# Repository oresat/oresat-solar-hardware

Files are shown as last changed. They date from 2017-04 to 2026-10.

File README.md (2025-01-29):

# OreSat Solar Modules

This repo contains the CAD for [OreSat's](oresat.org) solar modules. Part of OreSat's design is a module bus system that spans 1 - 3 U, so each array is its own 1U "panel". Oresat0, a 1U CubeSat, thus has 4 solar modules, and OreSat1, a 2U CubeSat, has 8. This approach has pretty severe drawbacks in terms of solar cell coverage area, but it's extremely flexible for having one design across a bunch of different designs. One nifty part of this design is that each 1u panel has its own **true** maximum power point tracker, with a software-defined MPPT algorithm. We're MPPT elitists - we eschew maximum power point "controllers" and think if it's not doing true power point optimization, you're just doing it wrong.

That and coffee. You're all doing coffee wrong, too, but we don't hold that against you, you don't live in Portland, we understand.

We've flown our GaAs solar cell design, and are currently workingon our silicon design.

# Design Notes

**Status, design, construction, and testing information can be found in the [OreSat Solar Module Design Notes](https://docs.google.com/document/d/1mogZjYhJievwLsnVkg4Q0sEF9xPMA5q7KPciky3YWKE/edit?usp=sharing).**

# Pretty Pictures

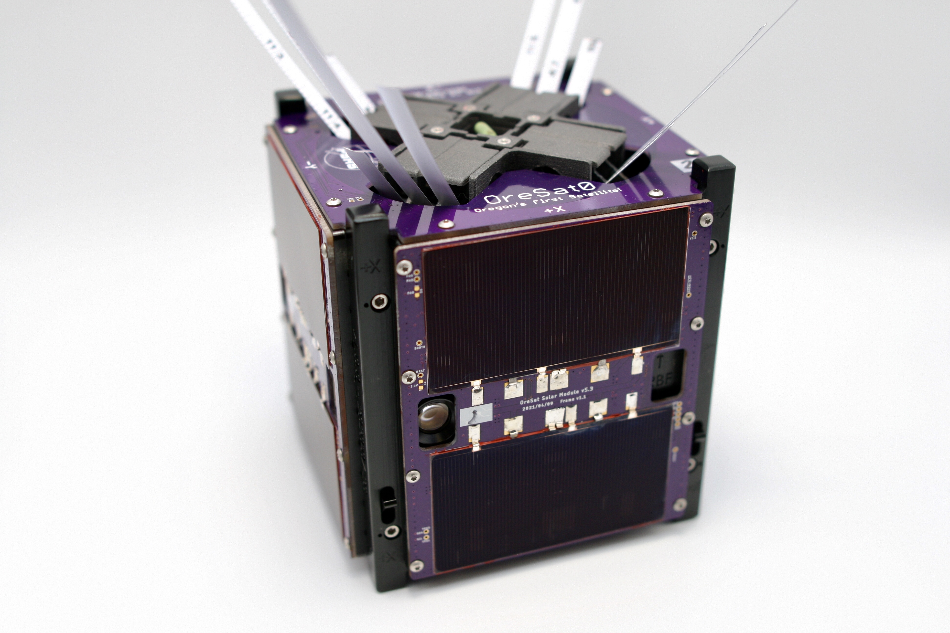
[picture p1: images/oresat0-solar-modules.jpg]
Solar modules on OreSat0

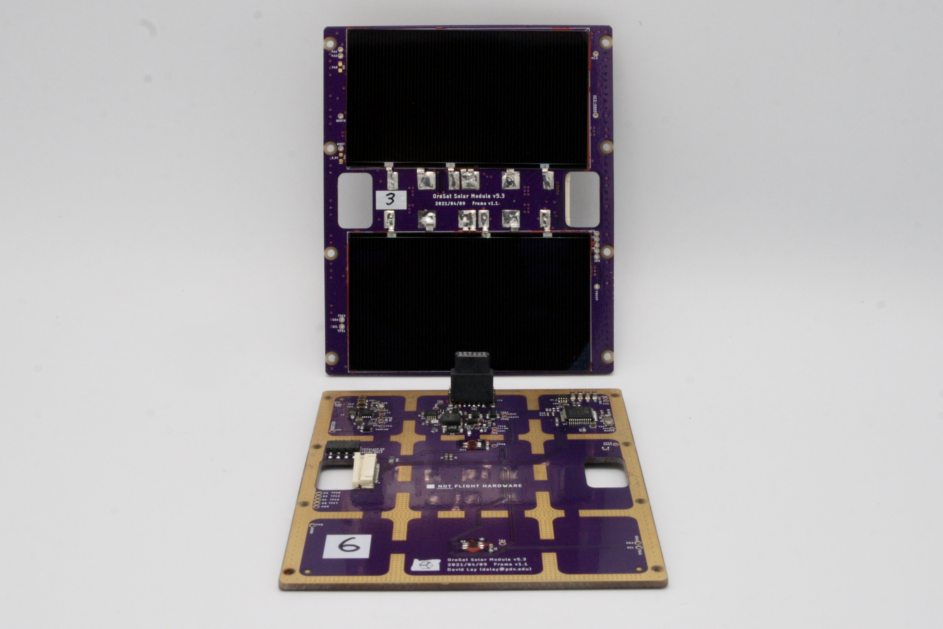
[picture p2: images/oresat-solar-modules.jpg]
Top (solar cells) and bottom (circuitry) of the solar modules


## LICENSE

Copyright the Portland State Aerospace Society, 2025.

This source describes Open Hardware that is licensed under CERN-OHL-S v2, or any later version.

You may redistribute and modify this source and make products using it under the terms of the CERN-OHL-S v2 (https://ohwr.org/cern_ohl_s_v2.txt).

This source is distributed WITHOUT ANY EXPRESS OR IMPLIED WARRANTY, INCLUDING OF MERCHANTABILITY, SATISFACTORY QUALITY AND FITNESS FOR A PARTICULAR PURPOSE. Please see the CERN-OHL-S v2 for applicable conditions.

Source location: https://github.com/oresat/

If you require a different license for this open hardware project, please contact us at [oresat@pdx.edu](mailto:oresat@pdx.edu).

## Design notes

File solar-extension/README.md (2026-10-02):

---
title: "**OreSat Solar Extension Board**"
subtitle: |
  **Fabrication and Assembly Information**\
  For build 2026-06-23T21-24-18
fontsize: 10pt
geometry:
  - margin=0.5in
toc: true
toc-depth: 2
colorlinks: true
urlcolor: blue
---

\newpage

# About this Board

## Board Description

This board connects the Oresat Solar Simulator to an OreSat engineering or development unit (specifically the End or Mid Cards). It allows us to plug HIL-run solar modules right into the engineering unit.

## Documentation Links

- Git repository: <https://github.com/oresat/oresat-solar-hardware>
- **TODO:** Design Notes + Design Review Notes

## Documentation Files

| Filename | Notes |
| --- | --- |
| README.pdf | This README file |
| flatsat-breakout-outline.dxf | Board outline (with holes) in DXF format |
| flatsat-breakout-pcba.step | 3D model of PCBA (with components) |
| flatsat-breakout-render-bot.jpg | Render of the top of the 3D model |
| flatsat-breakout-render-bot.jpg | Render of the bottom of the 3D model |
| flatsat-breakout-schematic.pdf | PDF of board schematics |

## Contact Information

- Website: <https://www.oresat.org/>
- Email: <oresat@pdx.edu>
- Instagram: @pdxaerospace

## Board Renders

Render of the top of the 3D model
Render of the bottom of the 3D model

\newpage

# Printed Circuit Board (PCB) Fabrication Information

## Board Info

- 2 layer board
- Bounding box is TBD
- Board thickness is 1.59 mm

## Board Requirements

- Design Rules
    - Minimum Trace / Space design rules
       - Outer layers: 0.127 mm (5.0 mil) / 0.127 mm (5.0 mil)
       - Inner layers: 0.127 mm (5.0 mil) / 0.127 mm (5.0 mil)
    - Outer dimension router tolerance: +/- 0.254 mm (10.0 mil)
    - Hole placement tolerance: +/- 0.075 mm (3.0 mil)
    - Inner tab routed slot tolerance: +/- 0.254 mm (10.0 mil)
- Drills
   - Drill Positional Tolerance: 0.051 mm (2.0 mil)
   - Drill Size tolerance: +/- 0.064 mm (2.5 mil)
- Plated/Un-plated holes
  - Via/PTH minimum diameter: 0.254 mm (10 mil)
  - Via/PTH minimum annulus: 0.102 mm (4 mil) radius
- Outline/Routing
  - No requirements
- Slots
  - There are no slots.
- Cutouts
  - There are no cutouts
- There are 3 fiducials on the top layer.
- Panel tabs ("mouse bites")
   - Card edges must be smooth; no mouse bites or other intrusions into the card outline.
   - If external mouse bites are required, minimize and customer will remove by hand before assembly.
- If not otherwise specified, build to IPC 6012 Class 2 or better.

## Stackup /  Materials

- Outside copper layers is 1 oz Cu after plating (0.043 mm / 1.7 mil)
- Inside copper layers are 0.5 oz Cu (0.018 mm / 0.7 mil)
- There are no requirements on the prepreg or core of this four layer stackup.
- Board Surface treatment should be ENIG, althogh immersion Silver is acceptable.
- White silkscreen on top and bottom surface
- Taiyo PSR-4000 or equivalent soldermask on top and bottom, no requirements for color.

## Array / Panel Information

- Coordinate with Contract Manufacturer (CM) for optimal size of this panel.
- If no feedback from CM, then produce single boards (no panel).

## Fabrication Files

### IPC-2581 File

| Filename | Notes |
| --- | --- |
| flatsat-breakout-ipc2581.xml | IPC-2581 board information file |

### Legacy PCB Files

| Filename | Notes |
| ---| --- |
| flatsat-breakout-Edge_Cuts.gbr | RS274X file for the dimension (outline) layer |
| flatsat-breakout-F_Silkscreen.gbr | RS274X file for the top silkscreen |
| flatsat-breakout-F_Mask.gbr | RS274X file for the top soldermask |
| flatsat-breakout-F_Cu.gbr | RS274X file for the top copper layer |
| flatsat-breakout-In1_Cu.gbr | RS274X file for the layer 2 copper |
| flatsat-breakout-In2_Cu.gbr | RS274X file for the layer 3 copper |
| flatsat-breakout-B_Cu.gbr | RS274X file for the bottom copper layer |
| flatsat-breakout-B_Mask.gbr | RS274X file for the bottom soldermask |
| flatsat-breakout-B_Silkscreen.gbr | RS274X file for the bottom silkscreen |
| flatsat-breakout-NPTH.drl | Excellon file for non-plated through holes |
| flatsat-breakout-PTH.drl | Excellon file for plated through holes | 

\newpage

# Printed Circuit Board Assembly (PCBA) Information

## Assembly Info

- This PCBA uses both surface mount (SMT) and through-hole (THT) components.

## Assembly Requirements

- Assemble to IPC Class 2 or better
- Bake components that are not moisture sealed to appropriate levels as required.
- Any solder paste (leaded or RoHS) is acceptable. RoHS solder is slightly preferred.
- Any no-clean or aqueous wash flux is acceptable.
- No conformal coating.

## Component Specific Assembly Information

- No specific information

## Assembly Files

### IPC-2581 File

| Filename | Notes |
| --- | --- |
| flatsat-breakout-ipc2581.xml | IPC-2581 board information file |

### Bill of Materials (BOM)

| Filename | Description |
| --- | --- |
| flatsat-breakout-bom.csv | BOM in Comma Separated Variable format |

### Solder Paste Stencils

| Filename | Notes |
| --- | --- |
| flatsat-breakout-B_Paste.gbr | RS274X file for top/front solder paste stencil |
| flatsat-breakout-F_Paste.gbr | RS274X file for bottom/back solder paste stencil |

### Mounting/Placement Location

| Filename | Description |
| --- | --- |
| flatsat-breakout.pos | Pick and place locations for components |

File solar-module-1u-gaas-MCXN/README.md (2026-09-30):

---
title: "**OreSat Solar Module with GaAs Cells and MCXN processor**"
subtitle: |
  **Fabrication and Assembly Information**\
  For build TIME-STAMP
fontsize: 10pt
geometry:
  - margin=0.5in
toc: true
toc-depth: 2
colorlinks: true
urlcolor: blue
---

\newpage

# About this Board

## Board Description

This PCB is for the OreSat "1U" solar module which is used for all OreSat 1 - 3U designs. It has GaAs and Si solar cell variants, as well as STM32 and MCXN microcontorller variants. This design is the GaAs + MCXN version. It is scheduled to fly on OreSat1. 

The solar module takes power from the solar cells and does true maximum power point tracking (MPPT) using the Perturb and Observe ("P&O") method. It boosts the cell voltage up to 8.2 V in order to directly charge the batteries.

## Documentation Links

- Git repository: <https://github.com/oresat/oresat-solar-hardware>
- [Design Notes](https://docs.google.com/document/d/1mogZjYhJievwLsnVkg4Q0sEF9xPMA5q7KPciky3YWKE/edit?usp=sharing)

## Documentation Files

| Filename | Notes |
| --- | --- |
| README.pdf | This README file |
| PROJECT-NAME-outline.dxf | Board outline (with holes) in DXF format |
| PROJECT-NAME-pcba.step | 3D model of PCBA (with components) |
| PROJECT-NAME-render-bot.jpg | Render of the top of the 3D model |
| PROJECT-NAME-render-bot.jpg | Render of the bottom of the 3D model |
| PROJECT-NAME-schematic.pdf | PDF of board schematics |

## Contact Information

- Website: <https://www.oresat.org/>
- Email: <oresat@pdx.edu>
- Instagram: @pdxaerospace

## Board Renders

Render of the top of the 3D model
Render of the bottom of the 3D model

\newpage

# Printed Circuit Board (PCB) Fabrication Information

## Board Info

- 4 layer board
- Bounding box is 83.0 x 100.0 mm
- Board thickness is 1.59 mm

## Board Requirements

- Design Rules
    - Minimum Trace / Space design rules
       - Outer layers: 0.127 mm (5.0 mil) / 0.127 mm (5.0 mil)
       - Inner layers: 0.127 mm (5.0 mil) / 0.127 mm (5.0 mil)
    - Outer dimension router tolerance: +/- 0.254 mm (10.0 mil)
    - Hole placement tolerance: +/- 0.075 mm (3.0 mil)
    - Inner tab routed slot tolerance: +/- 0.254 mm (10.0 mil)
- Drills
   - Drill Positional Tolerance: 0.051 mm (2.0 mil)
   - Drill Size tolerance: +/- 0.064 mm (2.5 mil)
- Plated/Un-plated holes
  - Via/PTH minimum diameter: 0.254 mm (10 mil)
  - Via/PTH minimum annulus: 0.102 mm (4 mil) radius
- Outline/Routing
  - This board requires a 1 mm router bit.
- Slots/Cutouts
  - There are six cutouts in the board.
- There are 3 fiducials on the top layer.
- Panel tabs ("mouse bites")
   - Card edges must be smooth; no mouse bites or other intrusions into the card outline.
   - If external mouse bites are required, minimize and customer will remove by hand before assembly.
- If not otherwise specified, build to IPC 6012 Class 2 or better.

## Stackup /  Materials

- Outside copper layers is 1 oz Cu after plating (0.043 mm / 1.7 mil)
- Inside copper layers are 0.5 oz Cu (0.018 mm / 0.7 mil)
- There are no requirements on the prepreg or core of this four layer stackup.
- Board Surface treatment should be ENIG, althogh immersion Silver is acceptable.
- White silkscreen on top and bottom surface
- Taiyo PSR-4000 or equivalent soldermask on top and bottom, no requirements for color.

## Array / Panel Information

- Coordinate with Contract Manufacturer (CM) for optimal size of this panel.
- If no feedback from CM, then produce single boards (no panel).

## Fabrication Files

### IPC-2581 File

| Filename | Notes |
| --- | --- |
| PROJECT-NAME-ipc2581.xml | IPC-2581 board information file |

### Legacy PCB Files

| Filename | Notes |
| ---| --- |
| PROJECT-NAME-Edge_Cuts.gbr | RS274X file for the dimension (outline) layer |
| PROJECT-NAME-F_Silkscreen.gbr | RS274X file for the top silkscreen |
| PROJECT-NAME-F_Mask.gbr | RS274X file for the top soldermask |
| PROJECT-NAME-F_Cu.gbr | RS274X file for the top copper layer |
| PROJECT-NAME-In1_Cu.gbr | RS274X file for the layer 2 copper |
| PROJECT-NAME-In2_Cu.gbr | RS274X file for the layer 3 copper |
| PROJECT-NAME-B_Cu.gbr | RS274X file for the bottom copper layer |
| PROJECT-NAME-B_Mask.gbr | RS274X file for the bottom soldermask |
| PROJECT-NAME-B_Silkscreen.gbr | RS274X file for the bottom silkscreen |
| PROJECT-NAME-NPTH.drl | Excellon file for non-plated through holes |
| PROJECT-NAME-PTH.drl | Excellon file for plated through holes | 

\newpage

# Printed Circuit Board Assembly (PCBA) Information

## Assembly Info

- All components are on the top side of the board.
- This PCBA uses only surface mount (SMT) components.

## Assembly Requirements

- Assemble to IPC Class 2 or better
- Bake components that are not moisture sealed to appropriate levels as required.
- Solder paste MUST be leaded.
- Aqueous flux and wash strongly preferred.
   - Clean to NASA Standard "Visibly Clean (VC)": No particles or residues are visible to the naked eye.
- No conformal coating.
- Ship in antistatic protective bag

## Component Specific Assembly Information

- U2 and U7 are hand installed upside down; see ["PSAS SOP - TMP101 Mounting on Solar MOdules"](https://docs.google.com/document/d/1C_-naV0ThPKOAYU6vSqqT_bxouM6lSOQ0vK8YNHYac8/edit?usp=sharing).
- Solar Cells D2 and D6 are hand placed; see ["PSAS SOP - Solar Cell mounting with PSA"](https://docs.google.com/document/d/1PRLbhDLpztdpU8TQuk0uR0zjref0UoxRCXlIfN_OXDI/edit?usp=sharing).

## Assembly Files

### IPC-2581 File

| Filename | Notes |
| --- | --- |
| PROJECT-NAME-ipc2581.xml | IPC-2581 board information file |

### Bill of Materials (BOM)

| Filename | Description |
| --- | --- |
| PROJECT-NAME-bom.csv | BOM in Comma Separated Variable format |

### Solder Paste Stencils

| Filename | Notes |
| --- | --- |
| PROJECT-NAME-B_Paste.gbr | RS274X file for top/front solder paste stencil |
| PROJECT-NAME-F_Paste.gbr | RS274X file for bottom/back solder paste stencil |

### Mounting/Placement Location

| Filename | Description |
| --- | --- |
| PROJECT-NAME.pos | Pick and place locations for components |

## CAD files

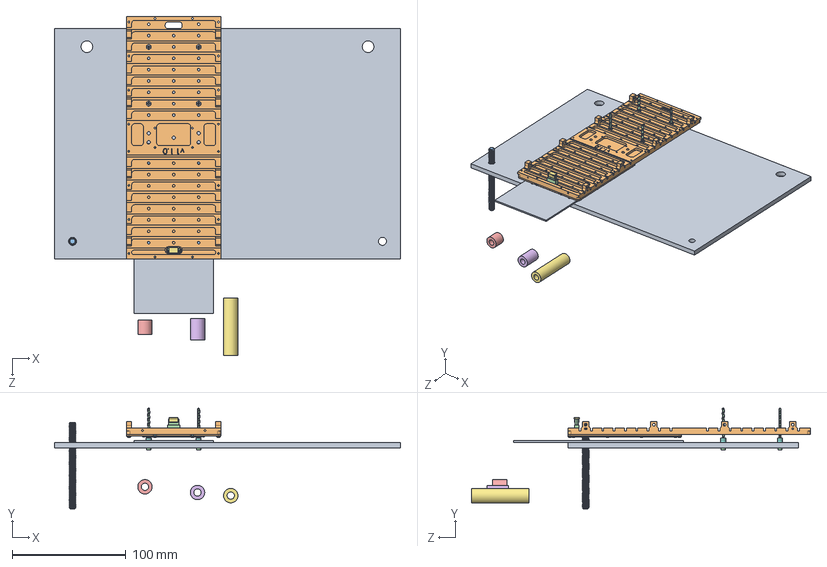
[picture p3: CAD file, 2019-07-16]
SolarSimulator/SolidWorks/solar testing full.SLDASM
304.8 x 88.6 x 299.0 mm
led mount
SolarModulePCB
ALTA-FIVE-CELL-THROUGH-SLOT
M55-60212_MOULD.stp
M55-602_CONTACT.stp x 12
M55-700_STRAP.stp x 2
90910A922_LOW-PROFILE BUTTON HEAD TORX MACHINE SCREW x 12
new led board
Y_Frame
93225A882_ALUMINUM THREADED ROD
91292A337_18-8 STAINLESS STEEL SOCKET HEAD SCREW x 4
92510A765_ALUM UNTHRD SPACER
92510A767_ALUM UNTHRD SPACER
92511A085_ALUM UNTHRD SPACER
92871A102_18-8 STAINLESS STEEL UNTHREADED SPACER x 8
91828A111_TYPE 18-8 STAINLESS STEEL HEX NUT x 4

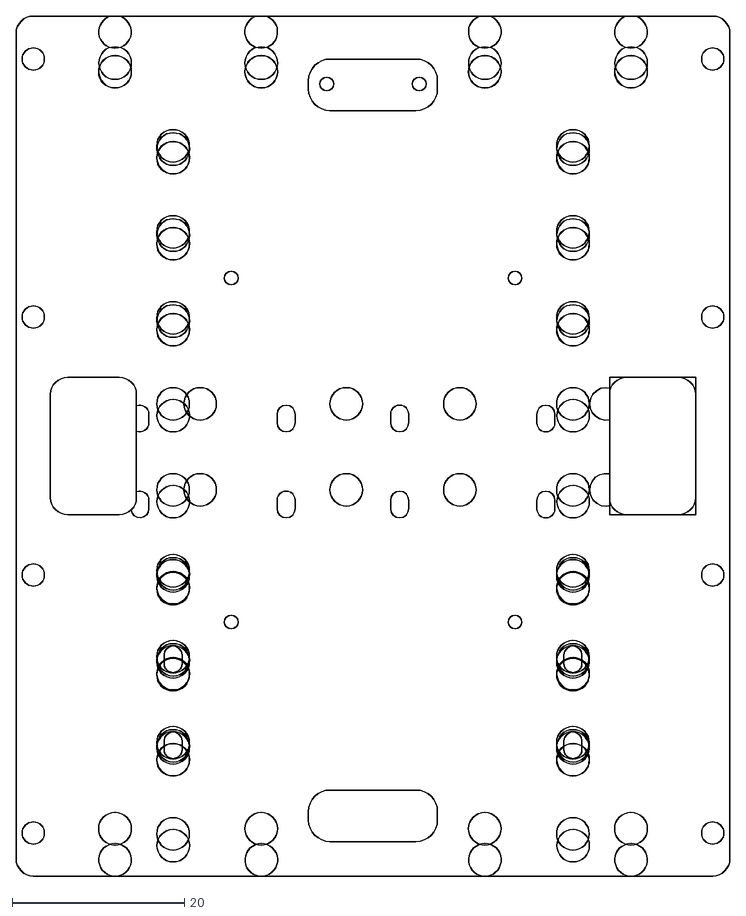
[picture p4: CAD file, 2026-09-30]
solar-module-1u-gaas-MCXN/Solar Module 2U and 3U DXF Sketch.dxf
83.0 x 100.0

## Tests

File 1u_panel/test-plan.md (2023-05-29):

# 1U Panel Test Plan

This assumes a completely assembled board, with a detailed visual inspection done that removes all visible shorts and corrects for any visually bad solder joints.

This testing assumes R24-R27 (CAN bus addresses) are not stuffed.

## Equipment

- Two channel power supply with constant current limit
- DMM
- Scope (50 MHz or better)
- SWD programmer for the STM32F091 (a debug cable, a Card Debug Board v2, and a laptop that can compile and program OreSat firmware).
- Two solar cell test panel with halogen bulb (or solar simulator).
- OreSat battery card (or any 2S Li ion battery pack) that is around 7.2 V, and definitely between 6.0 V and < 8.0 V.
- JouleScope with JouleScope software
- Temperature controlled hot air gun.

## Test Plan

In the following tests, do not continue to test if a test fails. Instead, debug the PCB then continue to test. If you don't fix these problems in order, you may end up destroying other circuits.
1. Circuit Test: Power
   1. Set: 5V @ 50 mA max into `Vsolar`.
   1. Measure: Solar module is drawing 13.5 +3/-1 mA.
      - Debugging notes: If the current draw is 50 mA, you have a short. Removing R17, R14, and R20 will let you identify where the short is. Hunt down the short in the downstream circuits using these three resistors. If the current draw is low, more debugging is necessary to determine the source of the error.
   1.Measure: 4.7V +/- 0.1V at `TP12`.
      - Debugging: The LT1618 should be off, so you'll just see the drop of D5. The LTC4412 may not work at 5V, so it's OK if `TP14` is weird.
   1. Measure: 3.3V +/- 5% at `TP6`. (TODO: ACTUAL PERCENTAGE ERROR)
      - That TPS63030 is notoriously hard to reflow, so if that's not working, probably reflow that IC or pull it and retry.
   1. Set: insert RBF jumper into J1.
   1. Measure: `TP6` should drop to near 0 V.
      * Debugging notes: This verifies the !SD circuit is working on the 3.3V supply.
   1. Set: Remove RBF jumper.
   1. Set: Pull `TP10` up to 3.3V @ 10 mA max.
   1. Measure: 8.4V +1%/-10% at `TP12`.
      * Debugging notes: The current limit on the LT1618 is set to very low, so it might current limit if there's any issue down the line towards Vbus.
   1. Measure: 8.4 V +1%/-10% at `TP14`.
   1. Set: Insert RBF jumper into J1 and put some load to ground from TP14 (about 10k).
   1. Measure: ~ 0 V on `TP14`.
      * Debugging notes: This verifies the !SD circuit is working on MPPT / 8.2V supply.
   1. Set: Remove RBF jumper.
   1. Set: remove power from `TP10`. 
   
2. Program microcontroller
   1. Set: 5V @ 50 mA max into `Vsolar`.
   1. Set: Make sure UART debugging is enable in firmware (TODO: HOW?!)
   1. Set: Program microcontroller using the SWD programmer.
      * Debugging Notes: make sure to do `make clean && make all` at least once before `make write`.
   1. Measure: LED D6 should be blinking.
   1. Measure: Reboot the microcontroller using the reset switch on the Card Debug board and look for serial console boot up message.

3. Functional Test: MPPT
   1. Set: hookup two cell test panel to `Vsolar`.
   1. Set: Turn on some amount of irradiance on the cell test panel to give it plenty of power to run, like 25% of 1 sun.
   1. Set: hook up battery pack to `Vbus` (or `TP14`) through JouleScope and run JouleScope software.
   1. Measure: some amount of power flowing into the battery pack when irradiance is reasonable.
   1. Set: Make irradiance go up and down.
   1. Measure: see amount of power flowing into the battery pack track the irradiance level.

3. Functional Test: Temperature
   1. Set: same setup as in (3) above.
   1. Measure: on serial debug output, temperature on both TMP101A is around room temperature (~ 25 C).
   1. Set: Adjust hot air gun down to ~ 100 C and apply hot air to each TMP101A.
   1. Measure: see the temperature on each TMP101A go up to ~ 100 C.

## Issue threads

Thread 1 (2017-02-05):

v1.0 issues

andrewgreenberg, 2017-02-05:
Well we did it again: no RGB LED. I'm. So. Disappointed. In. Us.

Also: add an output power LED. Silly, but for debugging, it would be informative. It'd show us if the SPV1040 is working (or not).

Obviously, all LEDs are NP on the gold boards.

# TODO:

Add the following:

 - [ ] RGB LED
 - [ ] Power LED
 - [x] Silkscreen board number area
 - [x] `!SHUTDOWN` line blocking diode
 - [ ] Fiducials
 - [ ] Decide what to do with the through-hole version of the Harting connector: add the holes, or just keep cutting off the leads to make it SMD assuming that part isn't available?
 - [x] Should add Vsolar to the debug breakout so you can power the whole module off that connector.
 - [x] BOOT0 (pin 31) on the STM32 needs to be pulled to ground (also, a test point).

andrewgreenberg, 2017-02-05:
Need a large silkscreen area for writing the board number on the board (on both sides)

andrewgreenberg, 2017-02-06:
OreSat !SHUTDOWN line needs a good blocking diode. Probably a full silicon diode, one with very little reverse leakage at high temperatures.

andrewgreenberg, 2017-02-11:
Duh: need fiducials if we send these out.

natronics, 2017-02-11:
Updated issue body with formatted checklist of sub-items.

Closed 2019-08-23.

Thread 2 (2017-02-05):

Need a solar module "programming and debug" board (easy intro EAGLE project!)

andrewgreenberg, 2017-02-05:
Make a small, 2 layer PCB that has a 2mm header that fits the solar module's 2mm RA programming receptacle. The programming board is inserted into the slots in the PCB from the "outside" of the cubesat and then hooks into the RA receptacle right at the edge of the "upper left" slot.

Features we'd like:

- LED on the DEBUG line so we can see a heartbeat (or whatever) on the uC.
- FTDI cable adapter for the UART, or an actual FTDI chip with USB Type microB connector.
- A reset switch.
- An LED on the 3.3V showing if we have 3.3V power or not.
- A 2x10 ARM SWD receptacle so we can program the uC.

Closed 2019-08-23.

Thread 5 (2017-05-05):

Schematic: BOOT 0 floating

kwilsonpdx, 2017-05-05:
This should go through a 10K Resistor to (gnd/vss?).

andrewgreenberg, 2017-08-15:
Fixed 1.1.

Closed 2017-08-15.

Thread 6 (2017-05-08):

1u_debug_breakout layout issue: TX->TX RX->RX

kwilsonpdx, 2017-05-08:
Hihi,

On the debug breakout board, the TX line is connected to the TX line of the 1u_panel MCU. The RX line is connected to the RX line of the MCU.

I think it should be: Rx->Tx   and Tx->Rx.

glennl, 2017-05-08:
Yes, you need to roll the signals...

- Glenn

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

--
Glenn Noel LeBrasseur
glenn.lebrasseur@gmail.com

andrewgreenberg, 2017-08-15:
I love you all, but you are all terribly, terribly wrong.

Closed 2017-08-15.

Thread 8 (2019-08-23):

Update BOM for v3

davidalay, 2019-08-23:
The BOM is missing a couple things for V3

andrewgreenberg, 2020-08-05:
out of date

Closed 2020-08-05.

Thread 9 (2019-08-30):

Missing indicator LEDs

davidalay, 2019-08-30:
Add indicator LEDs in the next rev to aid in development. Vsolar, 3.3V lines, anywhere else?

Closed 2020-08-05.

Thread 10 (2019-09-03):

Debug breakout button misconnected

davidalay, 2019-09-03:
The button on the reset line is misconnected so that it will always short to ground if the button is populated

andrewgreenberg, 2020-08-05:
out of date

Closed 2020-08-05.

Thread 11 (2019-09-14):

Feedback resistors on tps63070 wrong

davidalay, 2019-09-14:
Should be R1=470k R2=150k

Closed 2020-10-11.

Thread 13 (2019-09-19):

LTC4412 initialization state is wrong

davidalay, 2019-09-19:
The LTC4412 needs to be normally open upon initialization so that the LT1618 can't kill the onboard M0 by crashing the V-I curve.  Pull R19 to ground and connect the gate of the LTC4412 to a GPIO pin that is seperate from !shutdown_stm.

Closed 2020-08-05.

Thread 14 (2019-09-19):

INA 226 Vbus needs to be connected to Vin+

davidalay, 2019-09-19:
Vbus should be connected to Vin+ not Vin-.  Doesn't totally screw everything up for now, but probably not great.

Closed 2020-08-05.

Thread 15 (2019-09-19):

TPS63070 inductor too large

davidalay, 2019-09-19:
The inductor is 2.1mm tall and should be <=1.9mm so that it doesn't interfere with the oresat structure.

Closed 2020-10-22.

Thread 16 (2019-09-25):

LTC4412 needs an NFET

davidalay, 2019-09-25:
We screwed up.  The 3.3V on the gate isn't enough to trigger the PFET.  Need to redo the circuit with an N-channel that initializes in the correct direction.

Closed 2020-08-05.

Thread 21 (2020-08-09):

Replace debug connector with better one and figure out what to do about the height?

andrewgreenberg, 2020-08-09:
OMG the Wurth ones were just unusable garbage.

andrewgreenberg, 2020-08-10:
All versions of the Wurth connector are now replaced with the TE one. The question is, can we find a decent one that is < 2.0 mm? I've ordered a few to try out.

Closed 2020-10-21.

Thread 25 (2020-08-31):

Brown out on initialization

davidalay, 2020-08-31:
Upon initialization of the MPPT, the F0 browns out if a load is connected.  Current theory is that the LT1618 is pushing too much current, as the system defaults to max current and starving the 3.3V line.  The lt1618 enable pin gets stuck at ~1.7 V during the system brownout (threshhold is at 1V).  Perhaps a RC timer on that pin so that it takes time for the LT1618 to enable, giving the the F0 time to boot.

andrewgreenberg, 2020-08-31:
I'm not sure what you mean "upon initialization of the MPPT"?

Initializing the MPPT: When the M0 boots, the LT1618-ENABLE should be held low, disabling the LT1618, until the DAC is initialized and everything is ready. Then we SLOWLY bring up the LT1618 and go into MPPT mode. If the solar array voltage ever crashed below 4V, then we should stop MPPT mode and wait until we have more sunlight.

MPPT mode: If there's no load, the MPPT is going to immediately drive to 8.4V and sit there. If you attach a big load, suddenly, it might brown out because it doesn't have time to react. We always expect there to be batteries in the loop here, so the MPPTs don't have to deal with sudden loads.

davidalay, 2020-08-31:
It turned out that we were not holding the enable pin low for long enough to give the DAC time to initialize.  We implemented that and it seemed stable.  I am leaving the issue open for now though because I am not yet convinced we fully characterized/solved the problem.

What was happening is that when the array went from high irradiance, to low irradiance, back to high irraidance (simulating a BBQ roll) the system would brown out if any load was connected (this was with batteries on the bus), with the enable pin stuck at 1.7V.  If the load was removed, then replaced while the module was illuminated, the M0 would begin tracking normally.  We didn't think to measure cell voltage in the low irradiance mode, but AFAIK we don't have any software under voltage lockout on the lt1618 right now.

It is possible that the cell was illuminated enough from the ambient room light (we didn't think to fully darken them, we just turned off our giant halogen) that the tps63070 was able to keep the M0 partially powered, hence the enable pin being stuck 'high' (the cutoff for the tps63070 is 2V, which I believe the alta cells sit higher than that at under ambient lighting conditions).

I also think you are right about the MPPT not having time to keep up.  Our refresh rate was set arbitrarily slow so we could follow the tracking, so its possible that the M0 didn't have time to throttle the lt1618 before a brown out occurred.

davidalay, 2020-09-07:
This problem still persists when the light is dimmed and then brought back up.  The F0 does not reset, it gets 'stuck' with the 3.3V line not coming back up properly.  This is potentially a major issue

andrewgreenberg, 2025-01-31:
This is not an issue in the v5.3 or later, or v1.0 Si designs anymore. Not sure what this issue is, but we've never seen it. So I'm closing this issue.

Closed 2025-01-31.

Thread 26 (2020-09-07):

Add capacitor bank on the 3.3V line

davidalay, 2020-09-07:
Adding a capacitor bank on the 3.3V line will give the M0 more time to back off the power draw when the MPP drops.  Currently the MPP drops so quickly that the M0 can't keep up, so the MPPT has to sit a little bit behind the 'true' mpp.

Closed 2020-10-11.

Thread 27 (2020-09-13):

Verify the footprint of the flipped tmp101 sensor

davidalay, 2020-09-13:

Closed 2020-10-19.

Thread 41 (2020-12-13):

pretty big reverse current through the LTC4412 if the panels are shorted, looks like a dead short.  Maybe the FETS?

davidalay, 2020-12-13:

Closed 2021-01-28.

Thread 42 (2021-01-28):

fix 22uF cap attributes and update BOM

davidalay, 2021-01-28:

andrewgreenberg, 2025-01-31:
Fixed in KICAD.

Closed 2025-01-31.

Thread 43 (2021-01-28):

fix 1 MOhm attributes and BOM

davidalay, 2021-01-28:

andrewgreenberg, 2025-01-31:
Fixed in KICAD.

Closed 2025-01-31.

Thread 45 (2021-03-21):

Fix temperature sensor pins FOR THE LAST TIME

andrewgreenberg, 2021-03-21:

Closed 2021-03-22.

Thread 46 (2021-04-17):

Draw the 3.3V supply from the inductor side of the shunt

andrewgreenberg, 2021-04-17:
... so the M0 knows how much current it's taking.

andrewgreenberg, 2025-01-31:
Too hard to do (it's tight in that MPPT circuit), and the load from the uC shouldn't affect the main MPPTing even if we don't see it.

Closed 2025-01-31.

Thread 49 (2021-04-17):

Fix shunt in BOM

davidalay, 2021-04-17:

andrewgreenberg, 2025-01-31:
This was fixed.

Closed 2025-01-31.

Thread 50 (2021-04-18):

Breakout INA266 shunt resistor and add filtering components

andrewgreenberg, 2021-04-18:
The extra 0.1 ohm isn't great, but it's only 23 mW, and it allows us to separate the LT1618's probably noisier Rshunt from the INA's. Maybe add filter caps on both sides of the resistor to ground, too.

andrewgreenberg, 2025-01-31:
Nah, not going to add another shunt. We think sharing one is still OK. Filtering is added, so closing this bug.

Closed 2025-01-31.

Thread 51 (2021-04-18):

Probably change the shunt resistor to 1206 to match the OPD's shunt resistor

andrewgreenberg, 2021-04-18:

JackkP, 2025-03-04:
Resolved as part of https://github.com/oresat/oresat-solar-hardware/issues/53#issuecomment-2699161552 with https://github.com/oresat/oresat-solar-hardware/commit/47b24e66f7fb89ecd4242d7ba2f8470d87b6f23d

Closed 2025-03-04.

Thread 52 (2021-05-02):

putting out way less current than they should.  Most likely(hopefully) a firmware problem.

davidalay, 2021-05-02:

andrewgreenberg, 2025-01-31:
Latest analysis says that we're actually doing OK power generation wise with the GaAs cells. The issue here is clearly the MPPT algorithm, so I'm going to close this issue and open another.

Closed 2025-01-31.

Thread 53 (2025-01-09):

Bring up issues on the Silicon v1.0 design

andrewgreenberg, 2025-01-09:
Lots of small fixes:

- U4 (INA226) has the SDA and SCL lines swapped
- U4 (INA226) uses 100 ohm filter resistors, and should use 10 ohm or less. Also, see the datasheet, throw a capacitor on it.
- U2 and U11 (TMP101) are just... weird. Still! It's like a curse on this idea. Make the symbol match the pin out in the datasheet. Then fix the footprint to match, and make sure that the RIGHT PIN ONE is flagged. It's current wrong on the footprint. Also, while you're fixing the footprint, consider making that slot narrower to better grab the little SOT-23-6 feet.
- Q1 is in backward. Furthermore, there's is NO reason it needs to be a DMP3050. It's not like we use that anywhere else? So switch to a SOT-23 P channel transistor like our standard NTR4101.
- See the rest of the issues; I think they have very valid points, especially adding a separate shunt resistor for the INA226 and the LT1618. Sharing them is cute, but might be super noisy for the INA226.
- Add a white number area at LEAST on the component surface, but a small one on the side on the cell surface would be great.
-

andrewgreenberg, 2025-01-09:
Other notes:

- You can officially kill TP27, TP26, and TP28, TP29

JackkP, 2025-01-10:
Additional Comment, need to change the PN for the smaller cells in the middle from KXOB2502X8F to KXOB2502X8**T**F the difference being cell thickness. New PN is the thin revision from anysolar.

JackkP, 2025-01-29:
- ✅U4 (INA226)
    - ✅SDA and SCL connected to correct pins.
    - ✅Connected Vbus to Vin- (DS pg. 28).
    - ✅Reduced R36 and R37 to either zero ohms or 10 ohms. Added a 100n capacitor across them (DS pg.14).
    - 🛈 **Did not change footprint, current footprint matches datasheet recommended landing pattern (DS pg. 38).**
- ✅U3 (LT1618)
    - ✅Removed resistors R34 and R35.
    - ✅Check footprint, switched to oresat-ics:MSOP-10_ms to match recommended landing pattern
    - ✅Killed TP5
- ✅U2 and U11 are fixed
    - 🛈 Did *not update oresat-ics:DBV6-SLOT footprint (to adjust width). instead, changed the pins in the schematic symbol oresat-ics:TMP101NA; unclear why this was wrong, probably a symbol library conversion error. The pins in the DBV6-SLOT are correct for a slotted inverted IC, but the pins in the schematic symbol were also flipped.
- ✅Switched Q1 to NTR4101P.
- ❓Did not add a separate shunt for the INA226... can probably make space to do that if we think it's worthwhile. Do we want to do this?
- ✅Added white serial number areas on component surface and on cell surface
- ✅Updated  KXOB2502X8F to KXOB2502X8**T**F

These changes are resolved in [5202ddf](https://github.com/oresat/oresat-solar-hardware/commit/5202ddf4df5e114483215eab15eb4e8ec2a75c87)

**Things still needing review:**

- ❓Why is the refdes for the M55 connector CF1?
- ❓Is the white serial number area on the cell side satisfactory?
- ❓Did we figure out why V1.0 boards 1 and 6 have 💩 power output?
- ❓Add separate shunts for INA226 and `LT1618?`
- ⚠I need to thoroughly review the board before we do a design review and look for bad stuff

andrewgreenberg, 2025-01-31:
- Yeah, I think you really can kill those TPs. What do you want to review about it?
- CF1 stands for "Connector, Female". Feel free to change to "J"
- White serial number area is too big. Make it more "square". Big enough to hand-write a two digit number.
- We don't yet know about #1 and #6, will have to investigate, but that shouldn't slow down the v1.1 design.
- No, let's skip the separate shunts. I like sharing them until we figure out that sucks.
- OK, do the last minute review, I think we're good to go to try v1.1!

andrewgreenberg, 2025-02-02:
Just did a design review on these changes - https://docs.google.com/document/d/1YUit9oMjWgY5fHvdJ-Ph0KPl91w79ojY2p2lc8lckxo/edit?usp=sharing

JackkP, 2025-03-04:
- ✅Added 4.7uF caps to LTC4411s on solar cells
- ✅Vbus now goes to Vin+ on the INA226 (to calculate power from cells before rather than after shunt)
- ✅Cleaned up silkscreen
- ✅Added 3 ground test points (fix for https://github.com/oresat/oresat-solar-hardware/issues/47)
- ✅Removed TP26, TP27, TP28, TP29
- TMP101 Changes
     - ✅Added TMP101 datasheet to symbol
     - ✅Fixed TMP101 footprint to be 2.3mm wide
          - Increased length of pad by 0.05mm (inwards) to account for going from 2.4 to 2.3mm slot width... can we check the pads to see if they look good in DR?
     - 🛈 Updated symbol for TMP101 to use KiCad built in symbol
     - 🛈 Updated TMP101 foootprint pinout such that symbol matches IC and slotted footprint matches upside-down IC
- ✅Updated TCAN330 footprint to Package_TO_SOT_SMD:SOT-23-8
     - Pad size is slightly different, 1.35x0.5 instead of 1.1x0.45, but soldermask openings are smaller and pad corners are rounded... I think it should be better
- ✅Cleaned up all traces
- ✅Added 3 ground test points (fix for https://github.com/oresat/oresat-solar-hardware/issues/47)
- ✅Added 3D models for all missing components

JackkP, 2025-03-04:
Remaining Todos:

Todos:
- ⚠Move VSOLAR testpoint to be accessible from top surface
- Export 3D model to Onshape?
- ...?

Review: **THIS IS NOT EXHAUSTIVE (there's no such thing); IF YOU ARE REVIEWING LOOK FOR OTHER GARBAGE**
- Cells page:
     - Check Solar Cell LTC4411 circuits
          - Are caps on inputs and outputs correct?
          - Pinout check
          - Are the caps in the schematic that are associated with each ideal diode the correct ones in layout (mega OCD)
          - Check bypass R, input, output cap routing for all ideal diodes
     - Check silicon cells part numbers
          - Make sure that part numbers are for thin cells
          - Double check DPN
               - If anything is wrong make sure to update for ALL numbered library items
- Power page:
     - Check INA226
          - SCL/SDA
          - Vin sense pins
          - 10 ohm resistors ok?
          - Current sense routing & capacitor placement look good?
     - LT1618:
          - Check pinout
          - Check connections to shunt resistor
          - Check enable and Iadj signals
     - Ideal Diode
          - Is the Q1 pinout correct
          - Are all Q1 PNs correct?
          - Double check U12 pinout
     - No changes to 3.3V SPS, CF1, or RBF, but should check anyways
- MCU page:
     - Check the TMP101 pinout 1000 times
          - Check SCL and SDA!
          - Check if new symbol looks correct
          - Are there any other boards using the TMP101... if so, we should check those because the footprint was updated *INCLUDING PIN NUMBERS
     - Check TCAN330 CAN XCVR pinout
- Misc:
     - Check to make sure silkscreen SN box looks fine
     - Check all silkscreen text to make sure it's clear which component it references
     - Go through DRC 1e+40 times

JackkP, 2025-05-18:
Updating Todos from 3-30 design review + fixes from last commit + checking everything

Critical fixes: None
Important Fixes:
 - Moved the VSOLAR TP to a place accessible from the cell side of the PCB
 - Moved a do-no-good ground test point next to the 3.3v test point available on the cell-side of the PCB
 - Swaped 3D model of CF1 to actual version which is longerr
Whatever your mom fixes:
 - Unchecked “Exclude from simulation” for all of the test points and for the hardware
 - Flipped the 3D model of the TMP101 in the slotted footprint for funzies
Other To Do:
 - Last minute ERC + DRC cleanup, commit, and have Andrew fab.
      - Swapped R17 symbol to Kicad symbol

Checklist:
- ✅ Cells page:
     - ✅ Checked Solar Cell LTC4411 circuits
          - ✅ Caps on inputs and outputs are correct (technically don't need the 1uF cap on the input)
          - ✅ Pinout check
          - ✅ Caps in the schematic that are associated with each ideal diode match between layout and schematic (mega OCD)
          - ✅ Check bypass R, input, output cap routing for all ideal diodes
     - ✅ Checked silicon cells part numbers
          - ✅ Part numbers are for thin cells
          - ✅ Double checked DPN
          - **⚠ Worth noting that if we switched to a 4 cell per component configuration instead of 8 cell per component (could put two in series to maintain the ~4.5v output) we could reduce the number of LTC4411's by a factor of 2 and slightly increase power by 10-20mW (since more of each SMD cell is actually covered with solar cell)**
- ✅ Power page:
     - ✅ Check INA226
          - ✅ SCL/SDA
          - ✅ Vin sense pins seem to be configured correctly
          - ✅ 10 ohm resistors good
          - ✅ Current sense routing & capacitor placement looks good
     - ✅ LT1618:
          - ✅ Pinout looks good
          - ✅ Connections to shunt resistor look great
          - ✅ Enable and Iadj signals look fine
          - ✅ FB resistor values look good
     - ✅ Ideal Diode
          - ✅ Q1 pinout is correct
          - ✅ Double checked U12 pinout
- ✅ MCU page:
     - ✅ Check the TMP101 pinout 1000 times
          - ✅ Check SCL and SDA!
          - ✅ Check if new symbol looks correct
     - ✅ Checked TCAN330 CAN XCVR pinout
- Misc:
     - ✅ Checked to make sure silkscreen SN box looks fine
     - ✅ Checked all silkscreen text to make sure it's clear which component is referenced
     - ✅ Went through DRC 1e+40 times
     - ✅ Updated REVISION and ISSUE_DATE variables

**All Changes are reflected in <insert commit>**

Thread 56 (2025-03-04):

GaAs: v6 module CAD files

andrewgreenberg, 2025-03-04:
Now that's we've done the silicon modules, bring the best of the silicon modules into the GaAs design, and:

- Fix all of the EAGLE to KiCAD transition issues
- Add all of the 3D like in the Si module
- Switch cells out to the new GaAs cells found by ESI
- Probably finally ditch the old EAGLE CAD when done?

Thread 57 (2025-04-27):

Connect INA226/TMP101 ALERT pins to GPIO

ThirteenFish, 2025-04-27:
The ALERT pins have some neat capabilities, the one I'm most interested in being an interrupt when a one-shot conversion is completed. This would help with both correctness and reducing power consumption.

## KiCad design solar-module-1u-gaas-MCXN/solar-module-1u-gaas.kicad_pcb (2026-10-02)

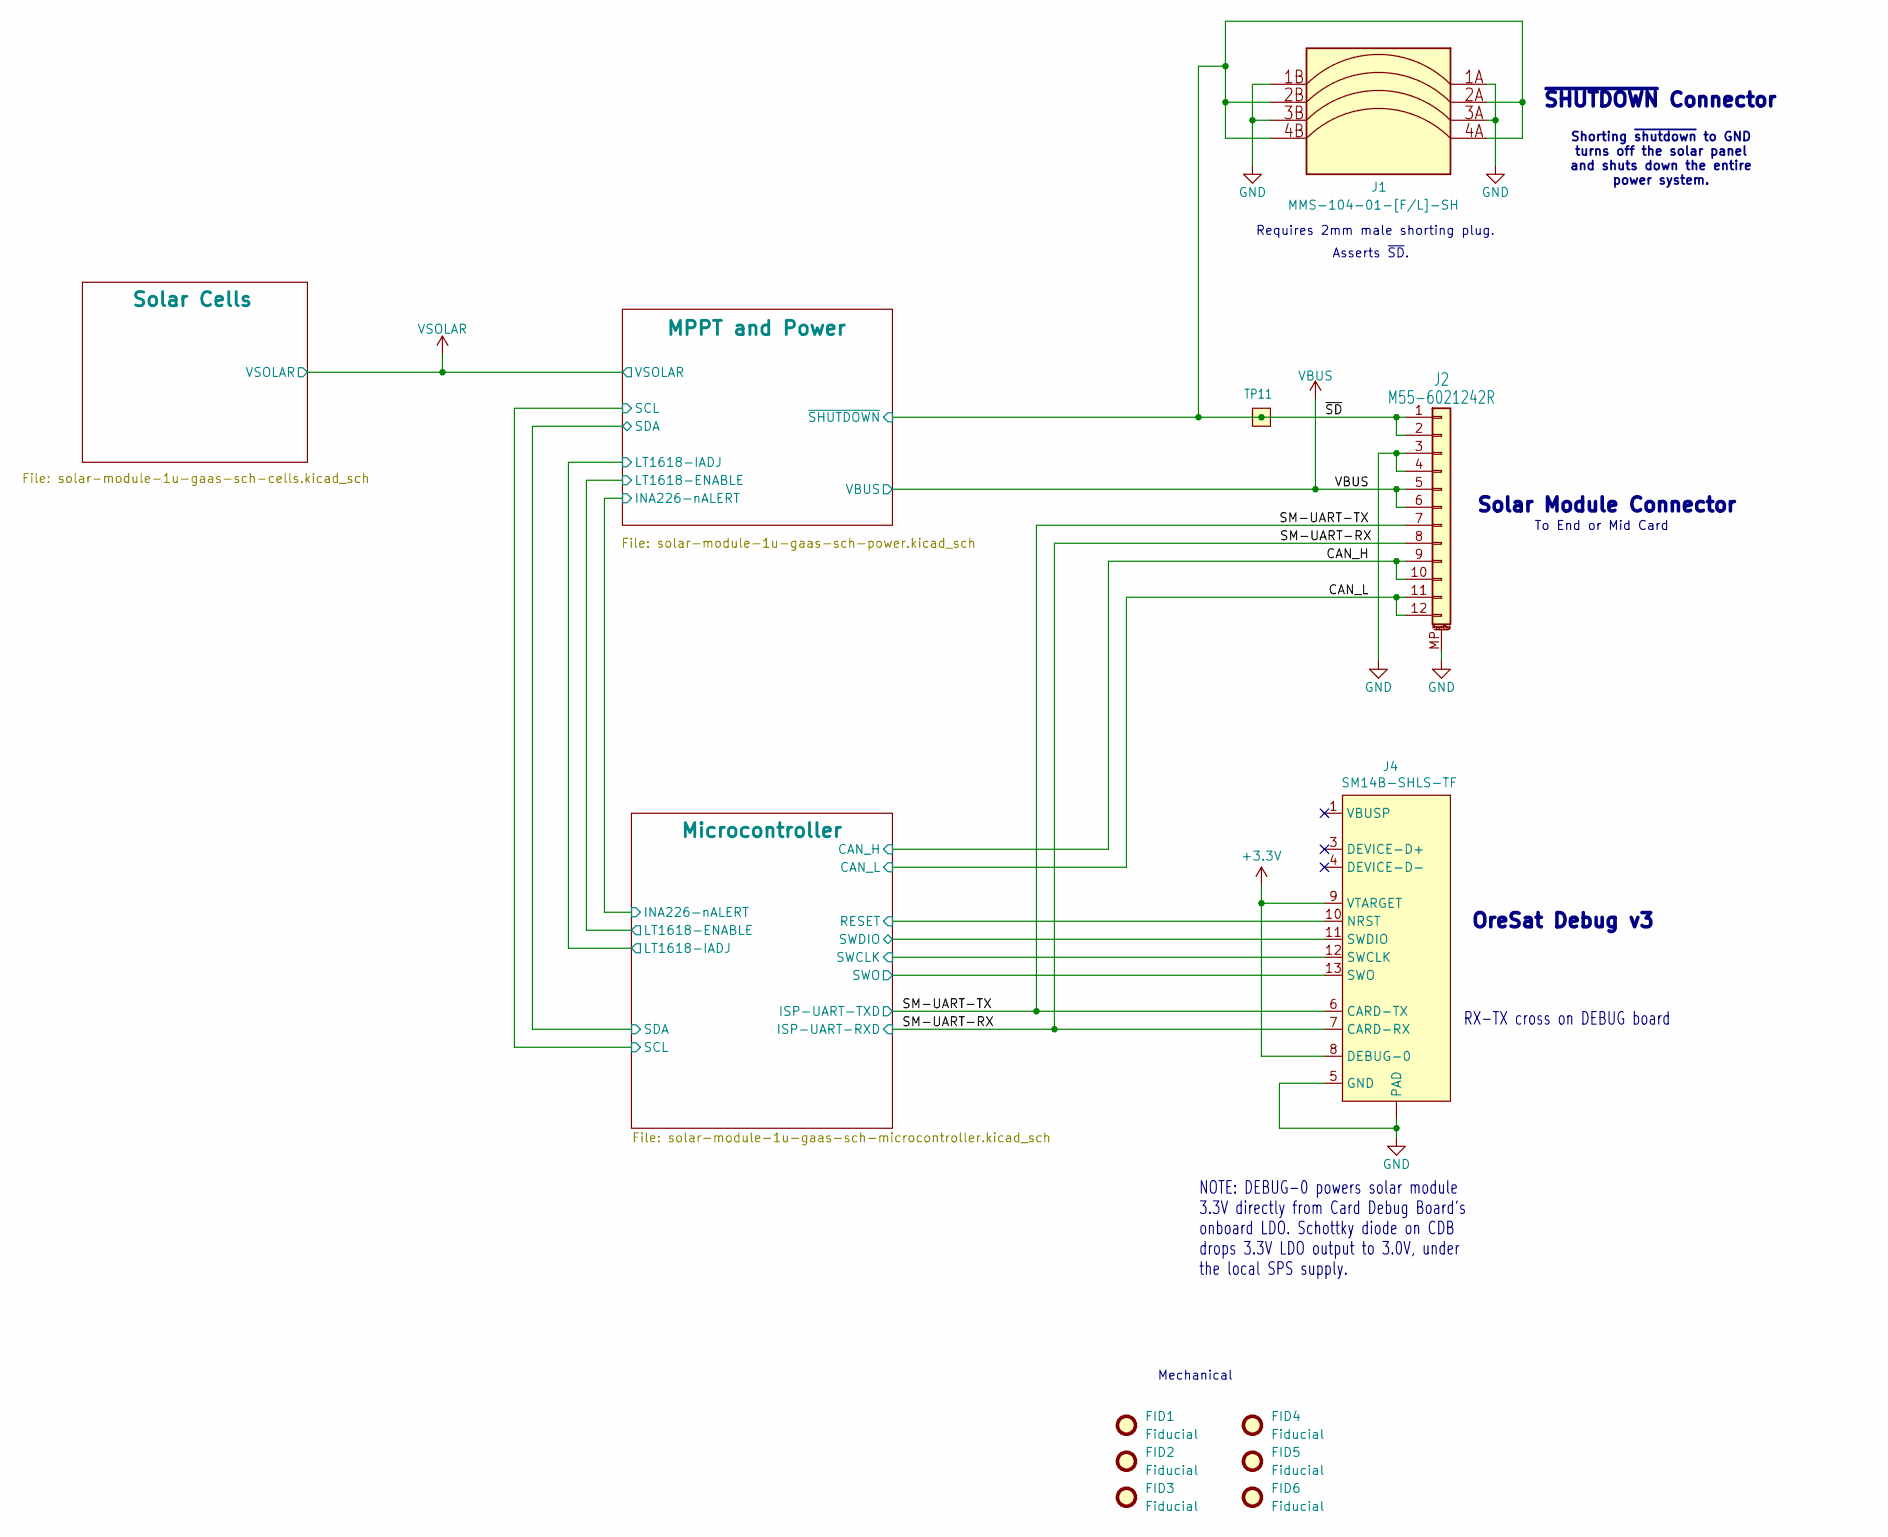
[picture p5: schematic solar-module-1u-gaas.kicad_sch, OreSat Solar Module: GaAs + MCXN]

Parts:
FID1, FID2, FID3, FID4, FID5, FID6: Fiducial; Fiducial_1mm_Mask2mm
J1: MMS-104-01-[F/L]-SH; SAMTEC-MMS-104-02-X-SH; MPN MMS-104-02-L-SH
J2: M55-6021242R; J-Harwin-M55-60X1242R; MPN M55-6021242R
J4: SM14B-SHLS-TF; J-JST-SM14BSHLSTF; MPN SM14B-SHLS-TF
TP11: TEST-POINT-LARGE-SQUARE; TestPoint-0.75mm-th

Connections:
+3.3V: J4.8 (DEBUG-0), J4.9 (VTARGET); also elsewhere on the board
/CAN_H: J2.9, J2.10; also elsewhere on the board
/CAN_L: J2.11, J2.12; also elsewhere on the board
/Microcontroller/RESET: J4.10 (NRST); also elsewhere on the board
/Microcontroller/SWCLK: J4.12 (SWCLK); also elsewhere on the board
/Microcontroller/SWDIO: J4.11 (SWDIO); also elsewhere on the board
/Microcontroller/SWO: J4.13 (SWO); also elsewhere on the board
/SM-UART-RX: J2.8, J4.7 (CARD-RX); also elsewhere on the board
/SM-UART-TX: J2.7, J4.6 (CARD-TX); also elsewhere on the board
/~SD: J1.2A, J1.2B, J1.4A, J1.4B, J2.1, J2.2, TP11.1 (1_1); also elsewhere on the board
GND: J1.1A, J1.1B, J1.3A, J1.3B, J2.3, J2.4, J2.MP (MountPin), J4.5 (GND), J4.14 (GND), J4.15 (PAD), J4.16 (PAD); also elsewhere on the board
VBUS: J2.5, J2.6; also elsewhere on the board

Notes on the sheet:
RX-TX cross on DEBUG board
Mechanical
Asserts ~{SD}.
Requires 2mm male shorting plug.
OreSat Debug v3
Solar Module Connector
Shorting ~{shutdown} to GND turns off the solar panel and shuts down the entire power system.
To End or Mid Card
NOTE: DEBUG-0 powers solar module 3.3V directly from Card Debug Board's onboard LDO. Schottky diode on CDB drops 3.3V LDO output to 3.0V, under the local SPS supply.
~{SHUTDOWN} Connector

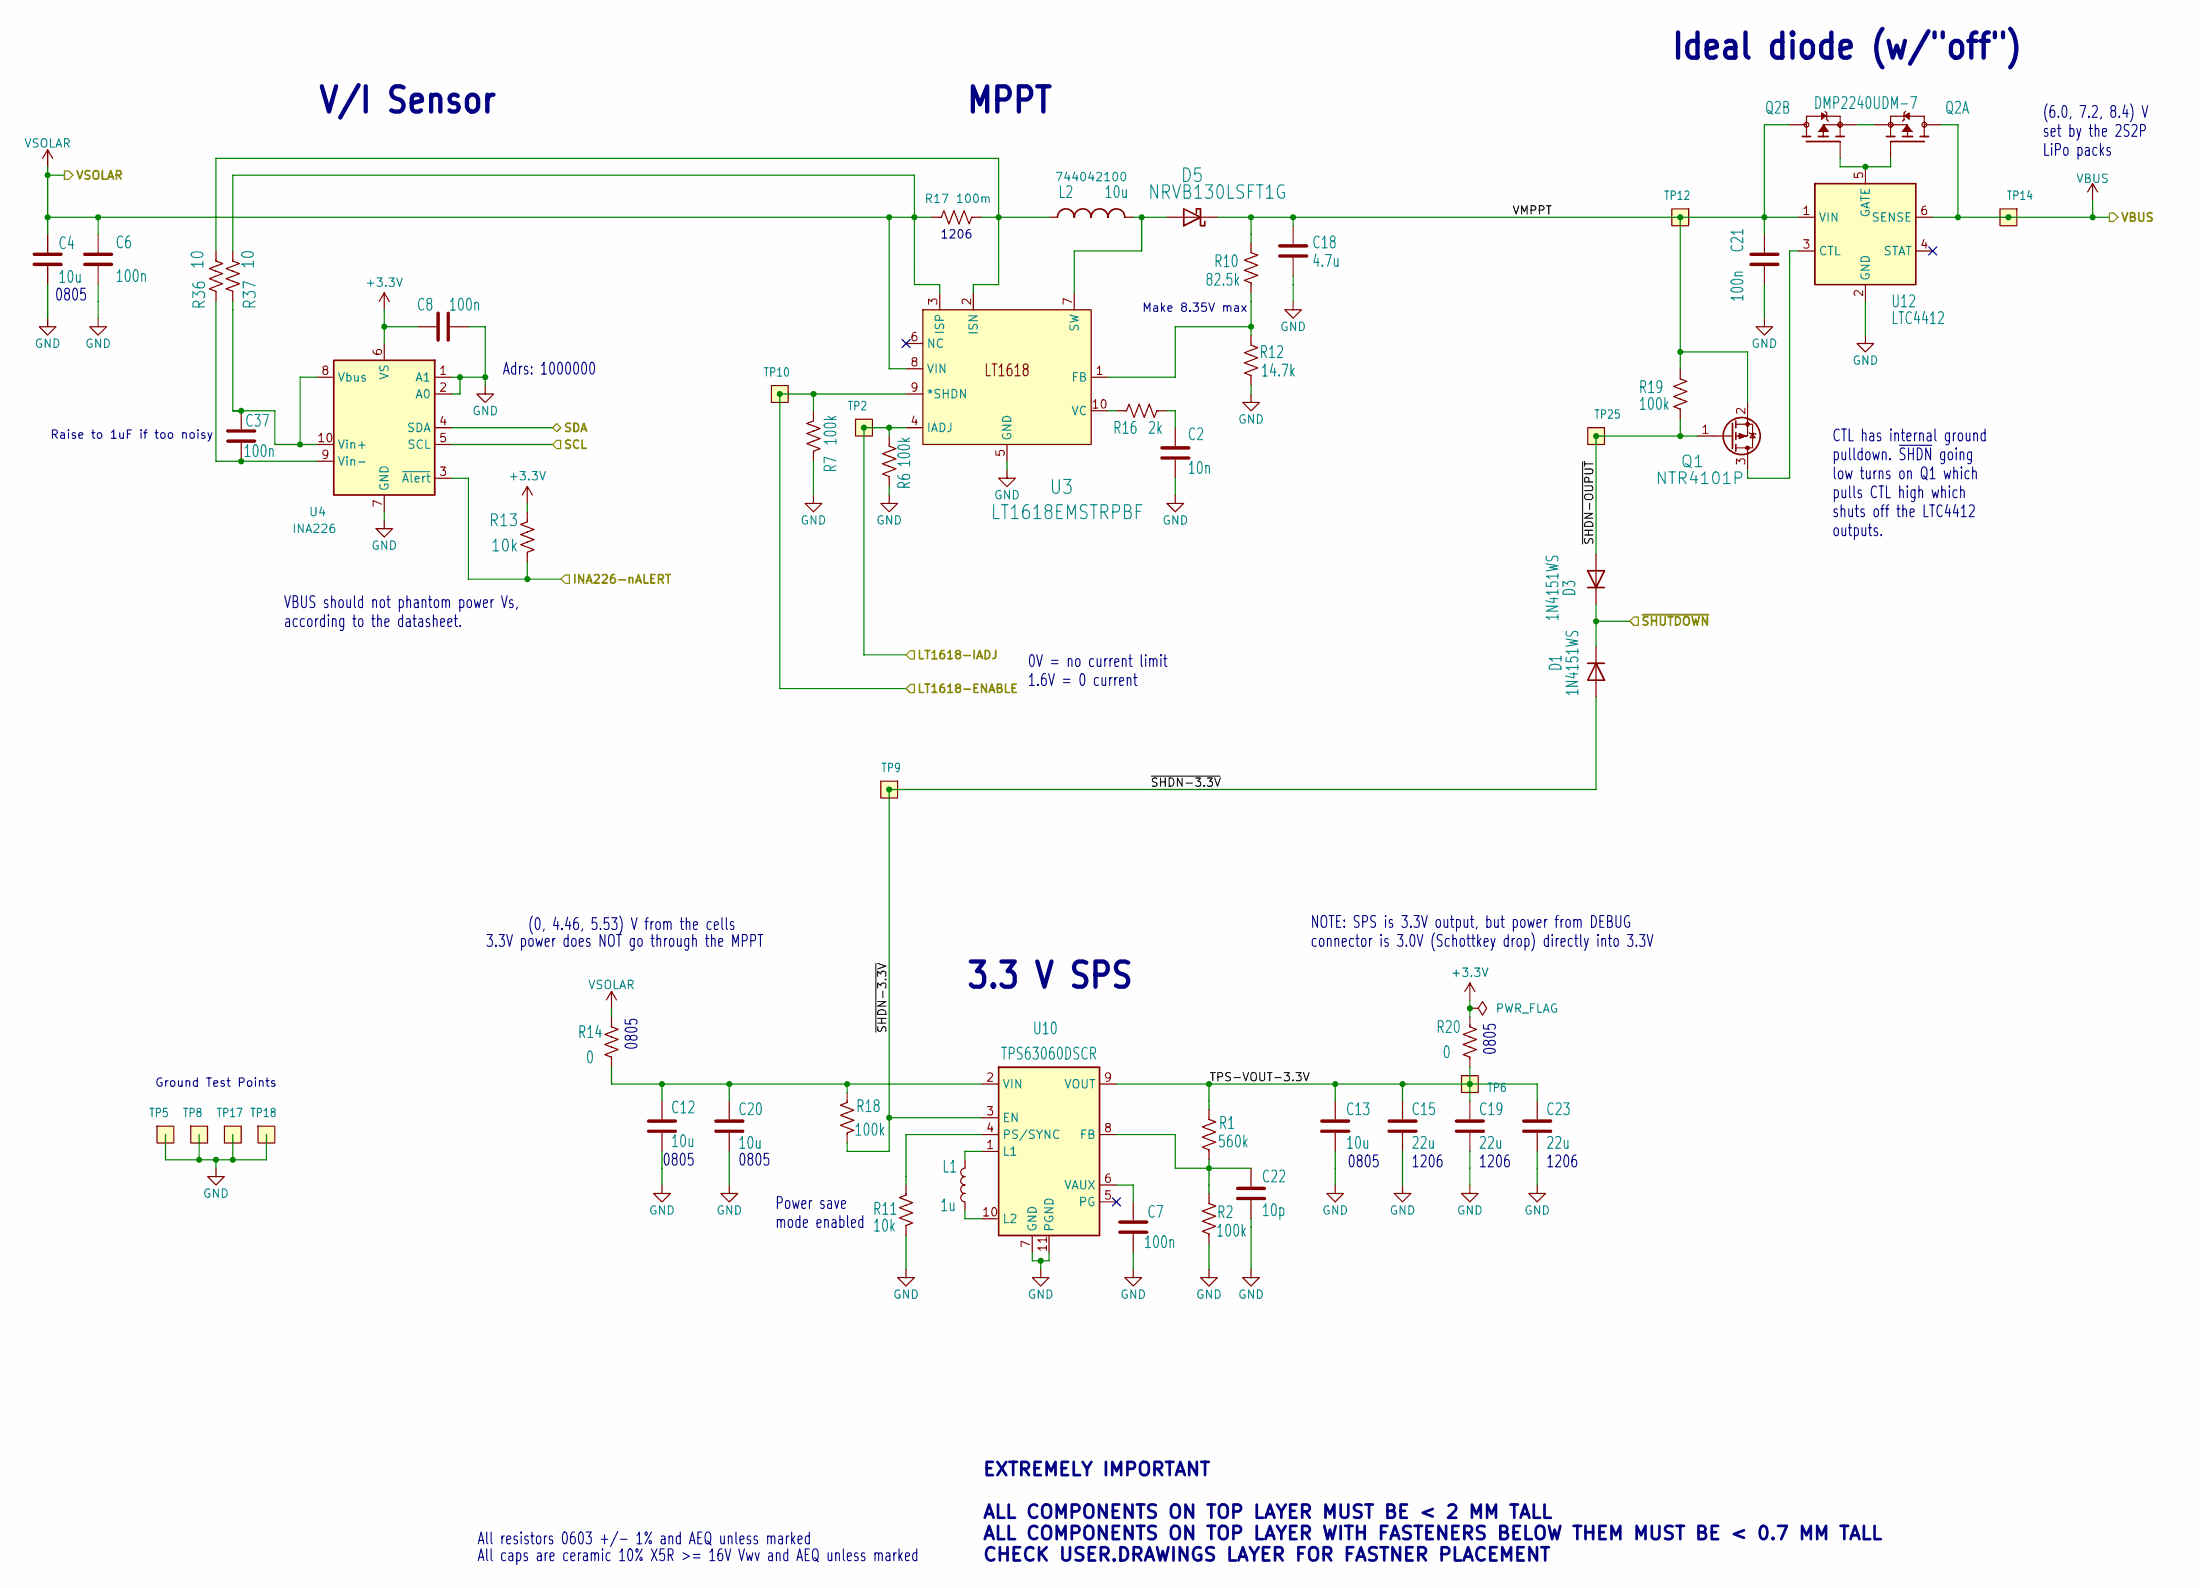
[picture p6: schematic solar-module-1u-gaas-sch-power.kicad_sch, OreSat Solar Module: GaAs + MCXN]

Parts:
C2: 10n; 0603-C-NOSILK; MPN C0603C103J5RACAUTO
C4, C12, C13, C20: 10u; 0805-C-NOSILK; MPN GRT21BC71E106KE13K
C6, C7, C8, C21, C37: 100n; 0603-C-NOSILK; MPN C0603C104K5RACAUTO
C15, C19, C23: 22u; 1206-C; MPN GRT31CC81C226KE01L
C18: 4.7u; 0603-C-NOSILK; MPN GRT188C71C475KE13D
C22: 10p; 0603-C-NOSILK; MPN C0603C100J1GACAUTO
D1, D3: 1N4151WS; D_SOD-323F; MPN 1N4151WS-E3-08
D5: NRVB130LSFT1G; D_SOD-123; MPN NRVB130LSFT1G
L1: 1u; IND_1226AS-H-1R0N=P2; MPN 1227AS-H-1R0N=P2
L2: 10u; 744042100; MPN 744042100
Q1: NTR4101P; SOT-23; MPN DMP2035UQ-7
Q2: DMP2240UDM-7; SOT-23-6; MPN DMP2240UDM-7
R1: 560k; 0603-C-NOSILK; MPN RMCF0603FT560K
R2, R6, R7, R18, R19: 100k; 0603-C-NOSILK; MPN RMCF0603FT100K
R10: 82.5k; 0603-C-NOSILK; MPN RMCF0603FT82K5
R11, R13: 10k; 0603-C-NOSILK; MPN RMCF0603FT10K0
R12: 14.7k; 0603-C-NOSILK; MPN RMCF0603FT14K7
R14, R20: 0; 0805-C-NOSILK; MPN RMCF0805ZG0R00
R16: 2k; 0603-C-NOSILK; MPN RMCF0603FT2K00
R17: 100m; 1206-C; MPN CSR1206FTR100
R36, R37: 10; 0603-C-NOSILK; MPN RMCF0603FT10R0
TP2, TP5, TP6, TP8, TP9, TP10, TP12, TP14, TP17, TP18, TP25: TEST-POINT-LARGE-SQUARE; TestPoint-0.75mm-th
U3: LT1618EMSTRPBF; MSOP-10_MS; MPN IC REG BOOST ADJ 1.5A 10MSOP
U4: INA226; TSSOP-10_3x3mm_P0.5mm; MPN INA226AIDGST
U10: TPS63060DSCR; Texas_S-PWSON-N10; MPN IC REG BUCK BOOST ADJ 2A 10WSON
U12: LTC4412; TSOT-23-6; MPN LTC4412ES6#TRPBF

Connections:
+3.3V: C8.1, R13.2, R20.1, U4.6 (VS); also elsewhere on the board
/MPPT and Power/INA226-nALERT: R13.1, U4.3 (~Alert); also elsewhere on the board
/MPPT and Power/LT1618-ENABLE: R7.1, TP10.1 (1_1), U3.9 (*SHDN); also elsewhere on the board
/MPPT and Power/LT1618-IADJ: R6.1, TP2.1 (1_1), U3.4 (IADJ); also elsewhere on the board
/MPPT and Power/TPS-VOUT-3.3V: C13.1, C15.1, C19.1, C23.1, R1.2, R20.2, TP6.1 (1_1), U10.9 (VOUT)
/MPPT and Power/VMPPT: C18.1, C21.1, D5.1 (K), Q1.2 (S), Q2.4 (D), R10.2, R19.2, TP12.1 (1_1), U12.1 (VIN)
/MPPT and Power/~SHDN-3.3V: D1.2 (A), R18.1, TP9.1 (1_1), U10.3 (EN)
/MPPT and Power/~SHDN-OUPUT: D3.2 (A), Q1.1 (G), R19.1, TP25.1 (1_1)
/Microcontroller/SCL: U4.5 (SCL); also elsewhere on the board
/Microcontroller/SDA: U4.4 (SDA); also elsewhere on the board
/~SD: D1.1 (K), D3.1 (K); also elsewhere on the board
GND: C2.2, C4.2, C6.2, C7.2, C8.2, C12.2, C13.2, C15.2, C18.2, C19.2, C20.2, C21.2, C22.2, C23.2, R2.1, R6.2, R7.2, R11.1, R12.1, TP5.1 (1_1), TP8.1 (1_1), TP17.1 (1_1), TP18.1 (1_1), U3.5 (GND), U4.1 (A1), U4.2 (A0), U4.7 (GND), U10.7 (GND), U10.11 (PGND), U12.2 (GND); also elsewhere on the board
unnamed: C2.1, R16.1
unnamed: D5.2 (A), L2.2, U3.7 (SW)
unnamed: Q1.3 (D), U12.3 (CTL)
unnamed: Q2.1 (G), Q2.3 (G), U12.5 (GATE)
unnamed: Q2.2 (S), Q2.5 (S)
unnamed: R10.1, R12.2, U3.1 (FB)
unnamed: L2.1, R17.2, R36.1, U3.2 (ISN)
unnamed: R16.2, U3.10 (VC)
unnamed: C37.1, R37.1, U4.8 (Vbus), U4.10 (Vin+)
unnamed: C37.2, R36.2, U4.9 (Vin-)
unnamed: C22.1, R1.1, R2.2, U10.8 (FB)
unnamed: L1.2, U10.1 (L1)
unnamed: L1.1, U10.10 (L2)
unnamed: R11.2, U10.4 (PS/SYNC)
unnamed: C7.1, U10.6 (VAUX)
unnamed: C12.1, C20.1, R14.1, R18.2, U10.2 (VIN)
VBUS: Q2.6 (D), TP14.1 (1_1), U12.6 (SENSE); also elsewhere on the board
VSOLAR: C4.1, C6.1, R14.2, R17.1, R37.2, U3.3 (ISP), U3.8 (VIN); also elsewhere on the board

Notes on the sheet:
1206
CTL has internal ground pulldown. ~{SHDN} going low turns on Q1 which pulls CTL high which shuts off the LTC4412 outputs.
(0, 4.46, 5.53) V from the cells
0805
Ground Test Points
Make 8.35V max
Raise to 1uF if too noisy
All resistors 0603 +/- 1% and AEQ unless marked
NOTE: SPS is 3.3V output, but power from DEBUG connector is 3.0V (Schottkey drop) directly into 3.3V
Power save mode enabled
3.3 V SPS
EXTREMELY IMPORTANT ALL COMPONENTS ON TOP LAYER MUST BE < 2 MM TALL ALL COMPONENTS ON TOP LAYER WITH FASTENERS BELOW THEM MUST BE < 0.7 MM TALL CHECK USER.DRAWINGS LAYER FOR FASTNER PLACEMENT
MPPT
All caps are ceramic 10% X5R >= 16V Vwv and AEQ unless marked
Ideal diode (w/"off")
VBUS should not phantom power Vs, according to the datasheet.
3.3V power does NOT go through the MPPT
V/I Sensor
0V = no current limit 1.6V = 0 current
Adrs: 1000000
(6.0, 7.2, 8.4) V set by the 2S2P LiPo packs

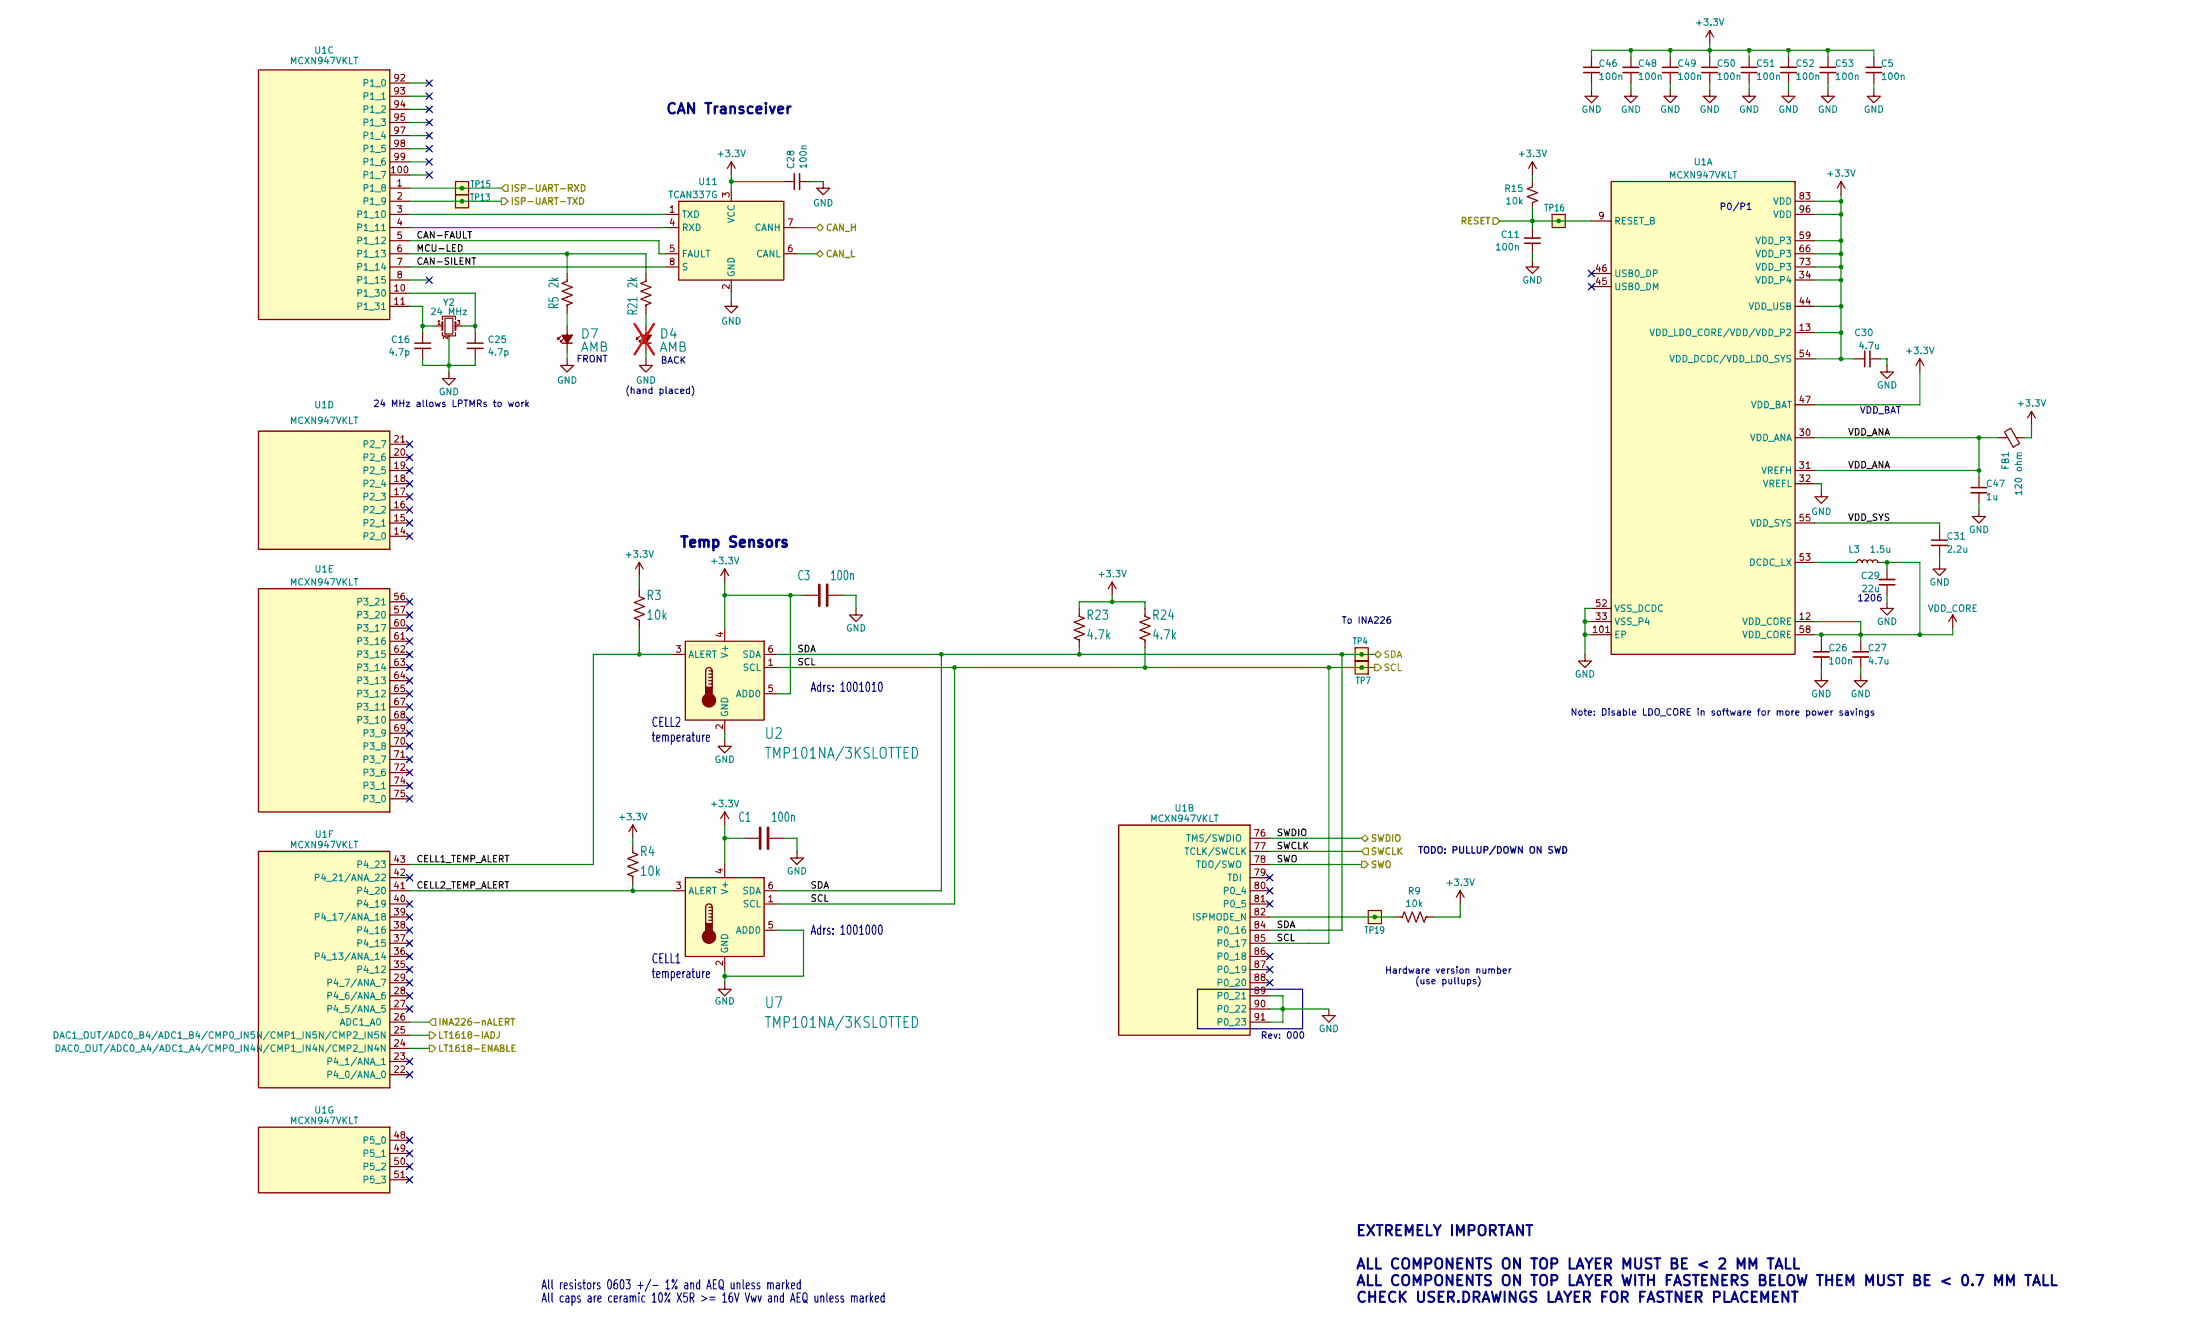
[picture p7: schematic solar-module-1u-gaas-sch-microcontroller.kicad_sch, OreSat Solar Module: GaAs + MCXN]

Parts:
C1, C3, C5, C11, C26, C28, C46, C48, C49, C50, C51, C52, C53: 100n; 0603-C-NOSILK; MPN C0603C104K5RACAUTO
C16, C25: 4.7p; 0603-C-NOSILK; MPN C0603C479D5GACAUTO
C27, C30: 4.7u; 0603-C-NOSILK; MPN GRT188C71C475KE13D
C29: 22u; 1206-C; MPN GRT31CC81C226KE01L
C31: 2.2u; 0603-C-NOSILK; MPN GRT188C71E225KE13D
C47: 1u; 0603-C-NOSILK; MPN GRT188R71E105KE13D
D4: AMB; LED_0603_1608Metric; MPN 150060AS75000; not fitted
D7: AMB; LED_0603_1608Metric; MPN 150060AS75000
FB1: 120 ohm; 0805-B-NOSILK; MPN 2508051217Y6
L3: 1.5u; L_0805_2012Metric; MPN SRP2012TMA-1R5M
R3, R4, R9, R15: 10k; 0603-C-NOSILK; MPN RMCF0603FT10K0
R5, R21: 2k; 0603-C-NOSILK; MPN RMCF0603FT2K00
R23, R24: 4.7k; 0603-C-NOSILK; MPN RMCF0603FT4K70
TP4, TP7, TP13, TP15, TP16, TP19: Test-Point; TestPoint-0.75mm-th
U1: MCXN947VKLT; MCXN947KVLT-QFP50P1600X1600X160-101N; MPN MCXN947VKLT
U2, U7: TMP101NA/3KSLOTTED; DBV6-SLOT; MPN TMP101NA/3K
U11: TCAN337G; SOT-23-8; MPN TCAN337GD
Y2: 24 MHz; Crystal_SMD_2016-4Pin_2.0x1.6mm; MPN 830108212309

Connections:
+3.3V: C1.1, C3.1, C5.1, C28.1, C30.1, C46.1, C48.1, C49.1, C50.1, C51.1, C52.1, C53.1, FB1.1, R3.2, R4.2, R9.2, R15.2, R23.2, R24.2, U1.13 (VDD_LDO_CORE/VDD/VDD_P2), U1.34 (VDD_P4), U1.44 (VDD_USB), U1.47 (VDD_BAT), U1.54 (VDD_DCDC/VDD_LDO_SYS), U1.59 (VDD_P3), U1.66 (VDD_P3), U1.73 (VDD_P3), U1.83 (VDD), U1.96 (VDD), U2.4 (V+), U2.5 (ADD0), U7.4 (V+), U11.3 (VCC); also elsewhere on the board
/CAN_H: U11.7 (CANH); also elsewhere on the board
/CAN_L: U11.6 (CANL); also elsewhere on the board
/MPPT and Power/INA226-nALERT: U1.26 (ADC1_A0); also elsewhere on the board
/MPPT and Power/LT1618-ENABLE: U1.24 (DAC0_OUT/ADC0_A4/ADC1_A4/CMP0_IN4N/CMP1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); also elsewhere on the board
/MPPT and Power/LT1618-IADJ: U1.25 (DAC1_OUT/ADC0_B4/ADC1_B4/CMP0_IN5N/CMP1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); also elsewhere on the board
/Microcontroller/CAN-FAULT: U1.5 (P1_12), U11.5 (FAULT)
/Microcontroller/CAN-SILENT: U1.7 (P1_14), U11.8 (S)
/Microcontroller/CELL1_TEMP_ALERT: R3.1, U1.43 (P4_23), U2.3 (ALERT)
/Microcontroller/CELL2_TEMP_ALERT: R4.1, U1.41 (P4_20), U7.3 (ALERT)
/Microcontroller/MCU-LED: R5.1, R21.1, U1.6 (P1_13)
/Microcontroller/RESET: C11.1, R15.1, TP16.1 (1_1), U1.9 (RESET_B); also elsewhere on the board
/Microcontroller/SCL: R24.1, TP7.1 (1_1), U1.85 (P0_17), U2.1 (SCL), U7.1 (SCL); also elsewhere on the board
/Microcontroller/SDA: R23.1, TP4.1 (1_1), U1.84 (P0_16), U2.6 (SDA), U7.6 (SDA); also elsewhere on the board
/Microcontroller/SWCLK: U1.77 (TCLK/SWCLK); also elsewhere on the board
/Microcontroller/SWDIO: U1.76 (TMS/SWDIO); also elsewhere on the board
/Microcontroller/SWO: U1.78 (TDO/SWO); also elsewhere on the board
/Microcontroller/VDD_ANA: C47.1, FB1.2, U1.30 (VDD_ANA), U1.31 (VREFH)
/Microcontroller/VDD_SYS: C31.1, U1.55 (VDD_SYS)
/SM-UART-RX: TP15.1 (1_1), U1.1 (P1_8); also elsewhere on the board
/SM-UART-TX: TP13.1 (1_1), U1.2 (P1_9); also elsewhere on the board
GND: C1.2, C3.2, C5.2, C11.2, C16.2, C25.2, C26.2, C27.2, C28.2, C29.2, C30.2, C31.2, C46.2, C47.2, C48.2, C49.2, C50.2, C51.2, C52.2, C53.2, D4.1 (K), D7.1 (K), U1.32 (VREFL), U1.33 (VSS_P4), U1.52 (VSS_DCDC), U1.89 (P0_21), U1.90 (P0_22), U1.91 (P0_23), U1.101 (EP), U2.2 (GND), U7.2 (GND), U7.5 (ADD0), U11.2 (GND), Y2.2 (G), Y2.4 (G); also elsewhere on the board
unnamed: D4.2 (A), R21.2
unnamed: D7.2 (A), R5.2
unnamed: L3.2, U1.53 (DCDC_LX)
unnamed: R9.1, TP19.1 (1_1), U1.82 (ISPMODE_N)
unnamed: C25.1, U1.10 (P1_30), Y2.3
unnamed: C16.1, U1.11 (P1_31), Y2.1
unnamed: U1.4 (P1_11), U11.4 (RXD)
unnamed: U1.3 (P1_10), U11.1 (TXD)
VDD_CORE: C26.1, C27.1, C29.1, L3.1, U1.12 (VDD_CORE), U1.58 (VDD_CORE)

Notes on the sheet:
To INA226
(hand placed)
Note: Disable LDO_CORE in software for more power savings
P0/P1
Temp Sensors
VDD_BAT
TODO: PULLUP/DOWN ON SWD
1206
CAN Transceiver
Adrs: 1001010
FRONT
Hardware version number (use pullups)
Adrs: 1001000
24 MHz allows LPTMRs to work
CELL2 temperature
EXTREMELY IMPORTANT ALL COMPONENTS ON TOP LAYER MUST BE < 2 MM TALL ALL COMPONENTS ON TOP LAYER WITH FASTENERS BELOW THEM MUST BE < 0.7 MM TALL CHECK USER.DRAWINGS LAYER FOR FASTNER PLACEMENT
Rev: 000
All resistors 0603 +/- 1% and AEQ unless marked
BACK
CELL1 temperature
All caps are ceramic 10% X5R >= 16V Vwv and AEQ unless marked

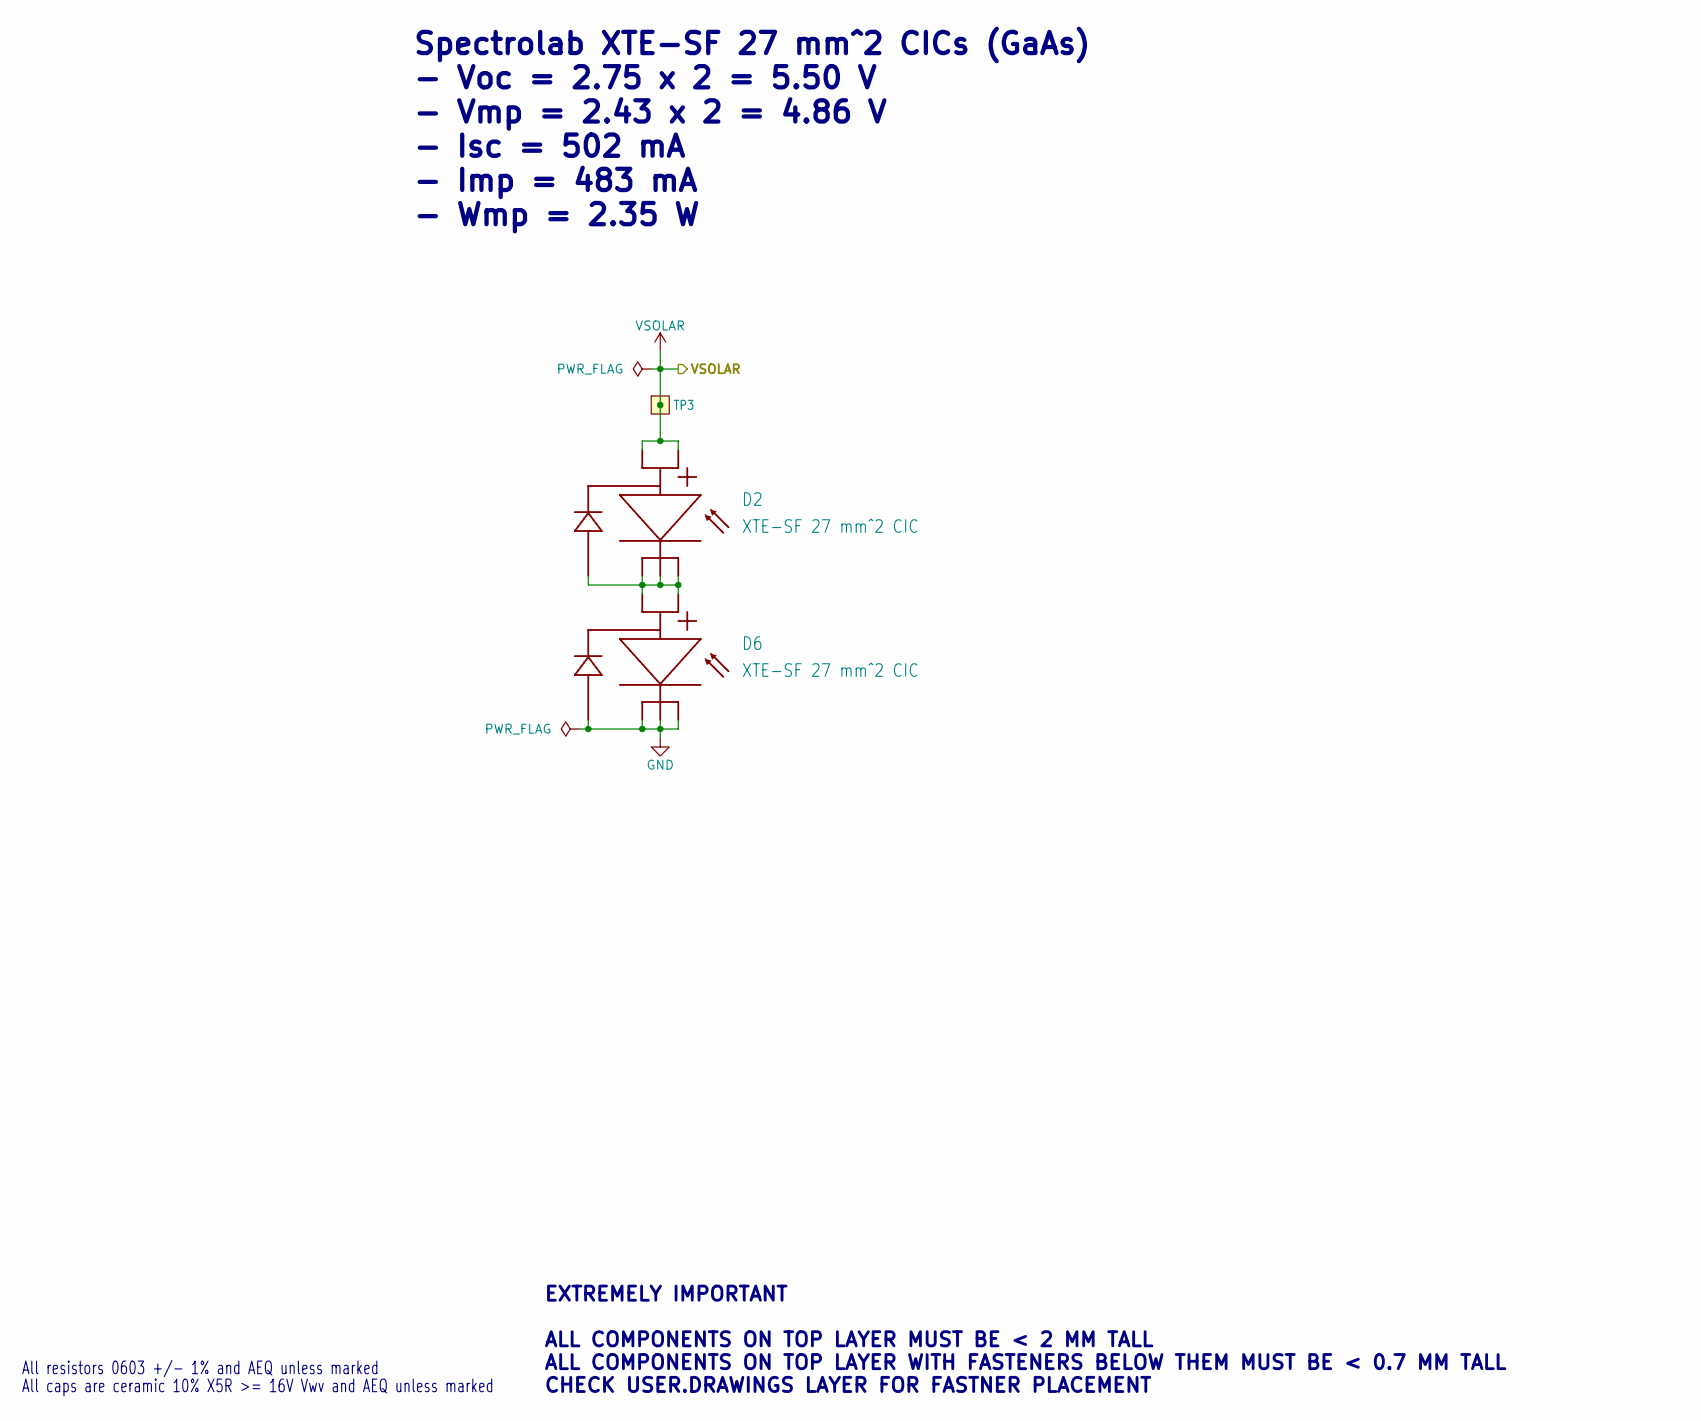
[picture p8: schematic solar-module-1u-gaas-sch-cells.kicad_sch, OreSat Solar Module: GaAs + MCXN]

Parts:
D2, D6: XTE-SF 27 mm^2 CIC; SPECTROLAB-XTE-SF-SLOTTED; MPN XTE-SF 27 mm^2 CIC
TP3: TEST-POINT-LARGE-SQUARE; TestPoint-0.75mm-th

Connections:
GND: D6.NEG1 (C1), D6.NEG2 (C2), D6.NEG3 (C3), D6.NEG4 (C4); also elsewhere on the board
unnamed: D2.NEG1 (C1), D2.NEG2 (C2), D2.NEG3 (C3), D2.NEG4 (C4), D6.POS1 (A1), D6.POS2 (A2)
VSOLAR: D2.POS1 (A1), D2.POS2 (A2), TP3.1 (1_1); also elsewhere on the board

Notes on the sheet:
All resistors 0603 +/- 1% and AEQ unless marked
Spectrolab XTE-SF 27 mm^2 CICs (GaAs) - Voc = 2.75 x 2 = 5.50 V - Vmp = 2.43 x 2 = 4.86 V - Isc = 502 mA - Imp = 483 mA - Wmp = 2.35 W
EXTREMELY IMPORTANT ALL COMPONENTS ON TOP LAYER MUST BE < 2 MM TALL ALL COMPONENTS ON TOP LAYER WITH FASTENERS BELOW THEM MUST BE < 0.7 MM TALL CHECK USER.DRAWINGS LAYER FOR FASTNER PLACEMENT
All caps are ceramic 10% X5R >= 16V Vwv and AEQ unless marked

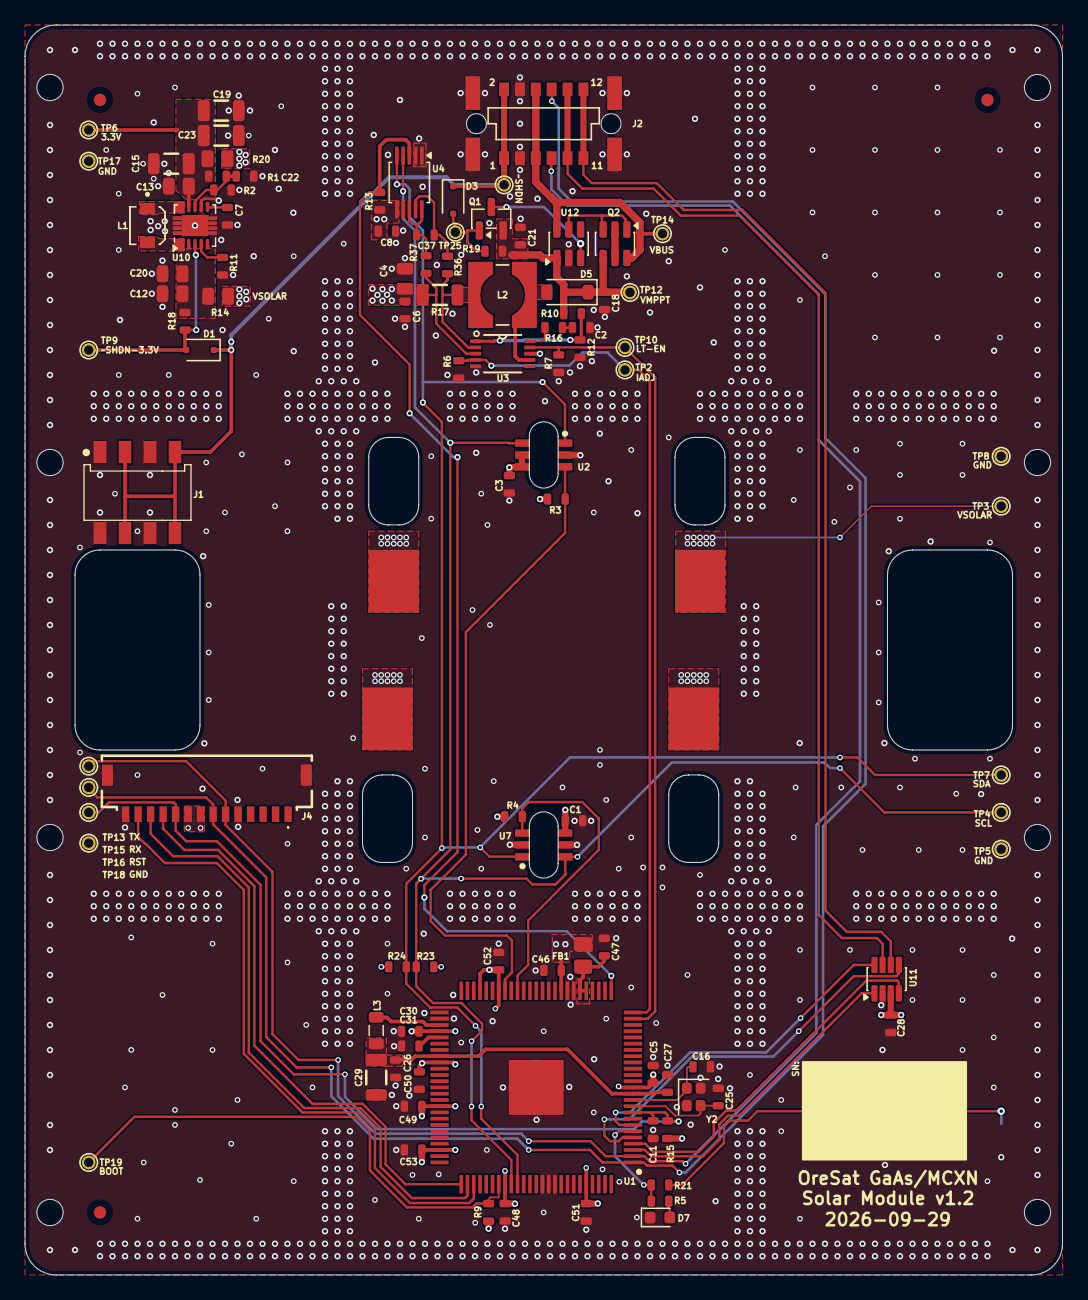
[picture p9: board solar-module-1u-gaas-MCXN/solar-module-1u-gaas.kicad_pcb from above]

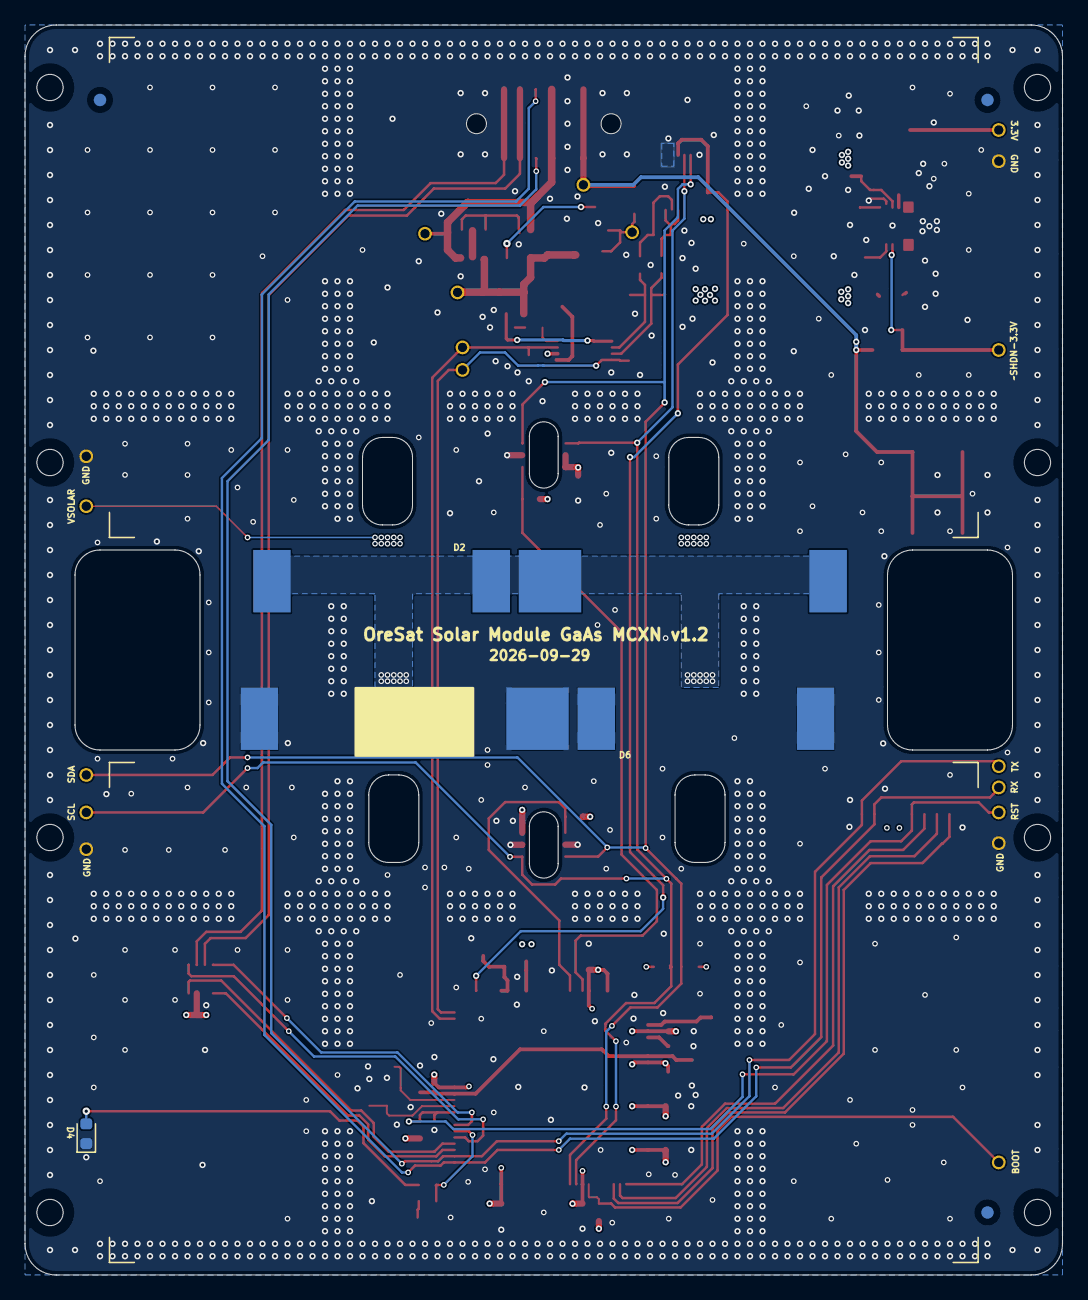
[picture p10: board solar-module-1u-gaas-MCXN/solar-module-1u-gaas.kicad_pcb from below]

Board: 4 copper layers, 83.0 x 100.0 mm, 110 parts (6 on the bottom side), 55 nets.

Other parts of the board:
PCB1: ORESAT-SOLAR-BOARD-V1.0-SILICON-CELLS; ORESAT-SOLAR-BOARD-V4

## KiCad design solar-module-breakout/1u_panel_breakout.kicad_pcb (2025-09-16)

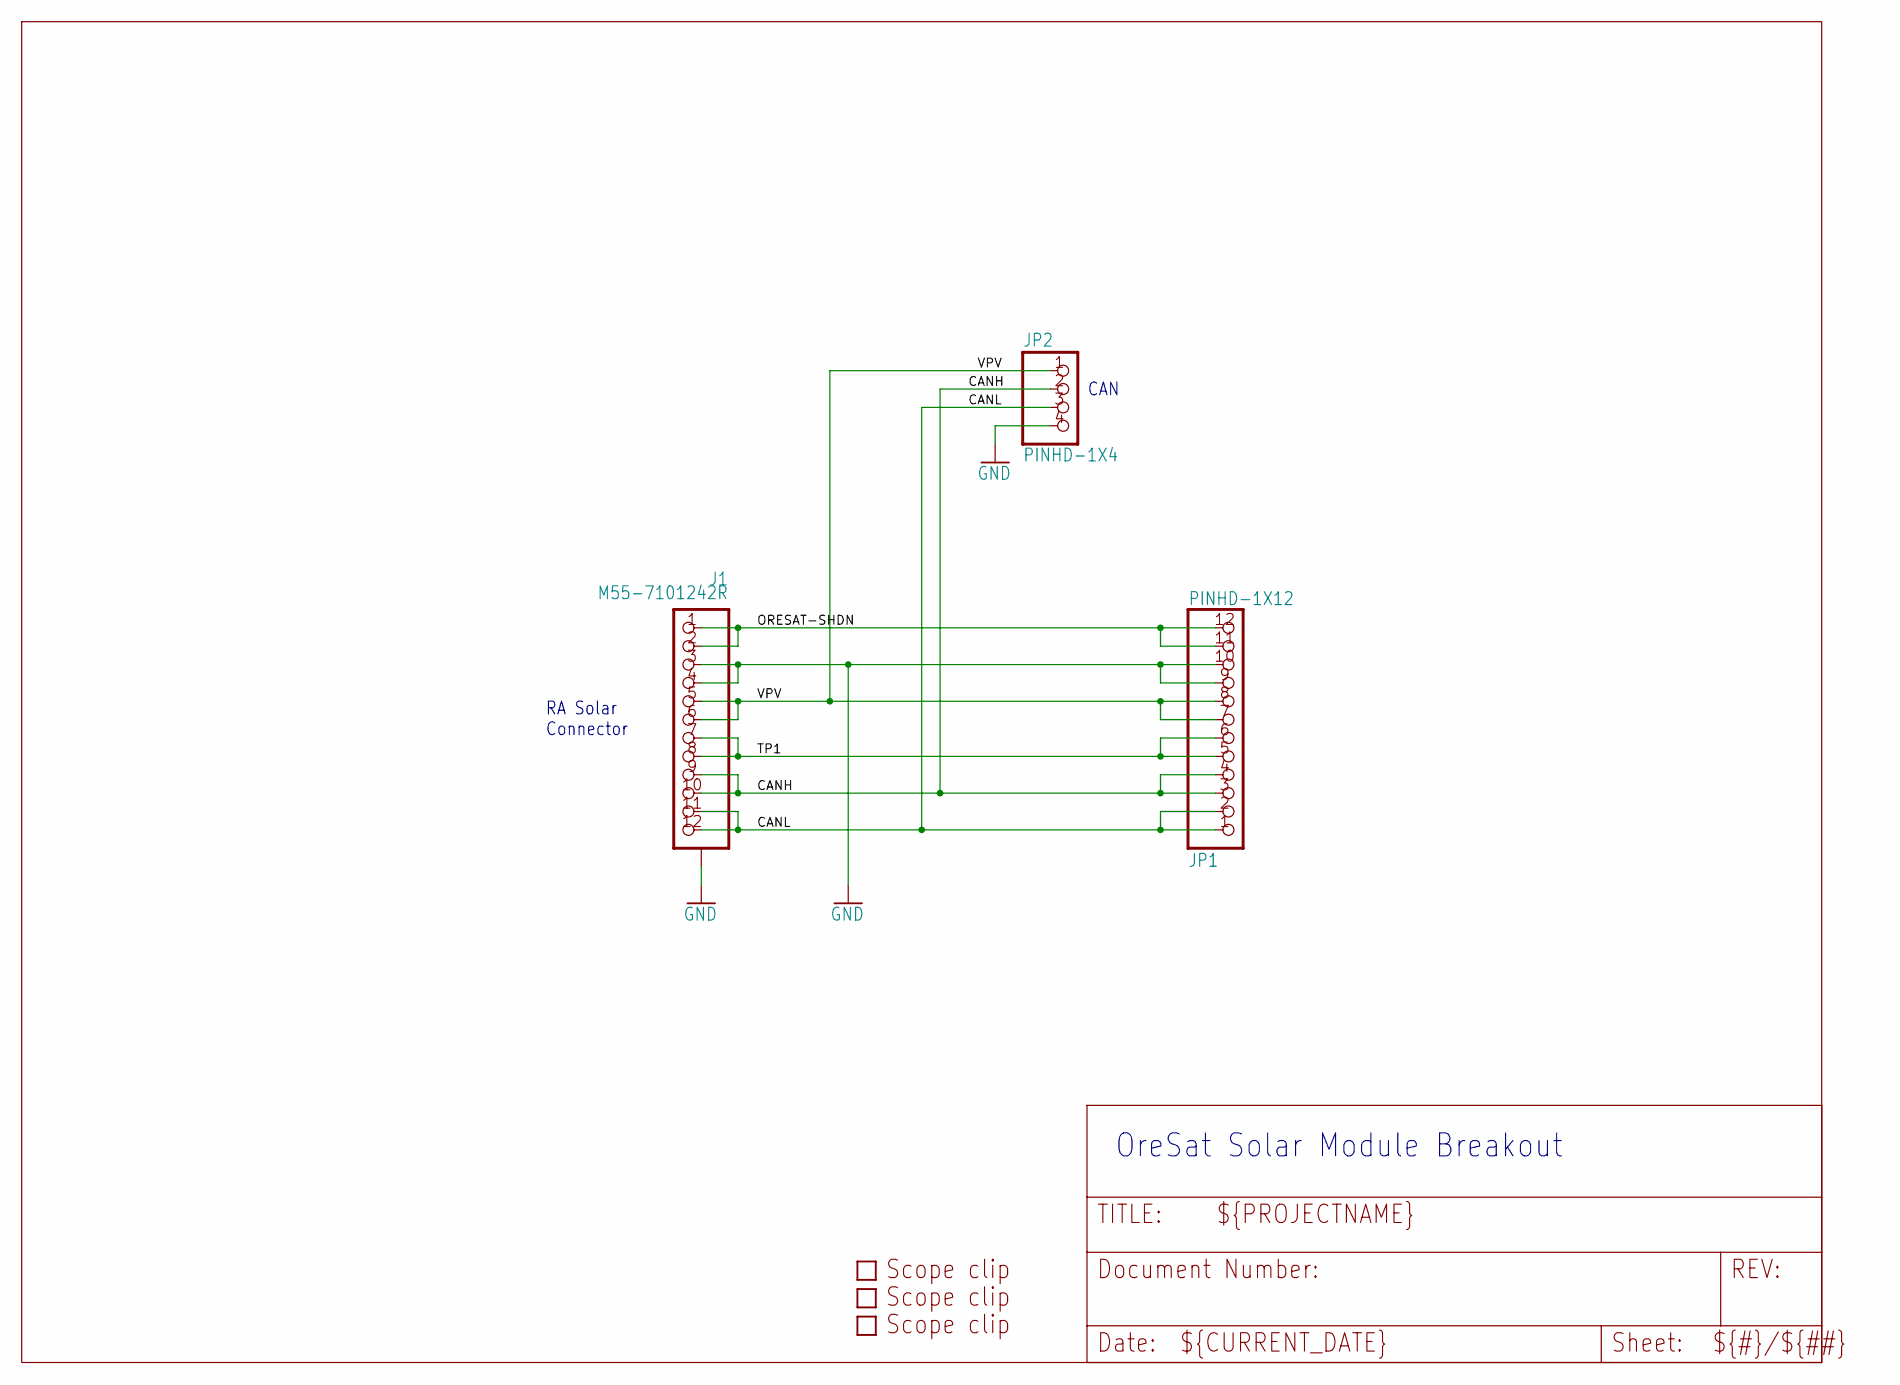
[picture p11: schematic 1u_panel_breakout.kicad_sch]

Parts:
J1: M55-7101242R
JP1: PINHD-1X12; 1X12
JP2: PINHD-1X4; 1X04
U$1, U$2, U$3: SCOPE_CLIP

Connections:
CANH: J1.9, J1.10, JP1.3, JP1.4, JP2.2
CANL: J1.11, J1.12, JP1.1, JP1.2, JP2.3
GND: J1.3, J1.4, J1.P$1 (SHIELD), J1.P$2 (SHIELD), J1.P$3 (SHIELD), J1.P$4 (SHIELD), JP1.9, JP1.10, JP2.4
ORESAT-SHDN: J1.1, J1.2, JP1.11, JP1.12
TP1: J1.7, J1.8, JP1.5, JP1.6
VPV: J1.5, J1.6, JP1.7, JP1.8, JP2.1

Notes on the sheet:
CAN
OreSat Solar Module Breakout
RA Solar Connector

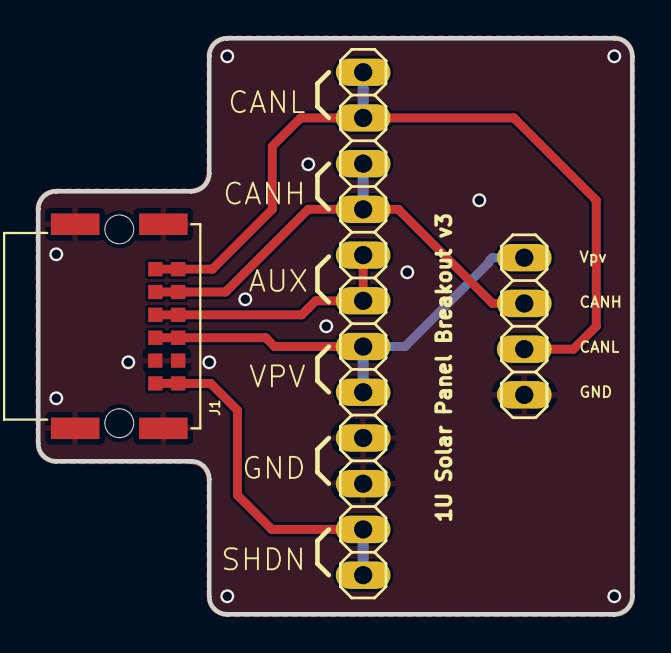
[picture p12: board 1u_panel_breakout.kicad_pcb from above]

Board: 2 copper layers, 33.0 x 32.0 mm, 6 parts (0 on the bottom side), 6 nets.

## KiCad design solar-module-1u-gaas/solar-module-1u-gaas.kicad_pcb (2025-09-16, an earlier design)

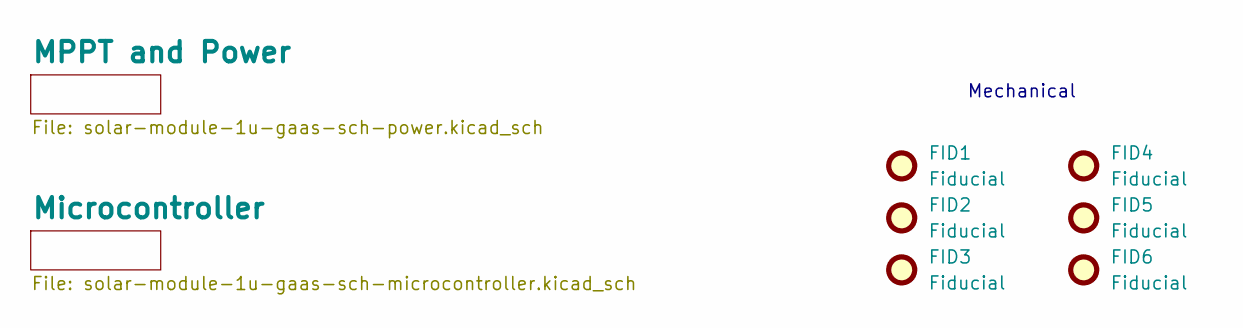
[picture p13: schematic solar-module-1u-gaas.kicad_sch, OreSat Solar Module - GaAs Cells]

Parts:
FID1, FID2, FID3, FID4, FID5, FID6: Fiducial; Fiducial_1mm_Mask2mm

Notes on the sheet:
Mechanical

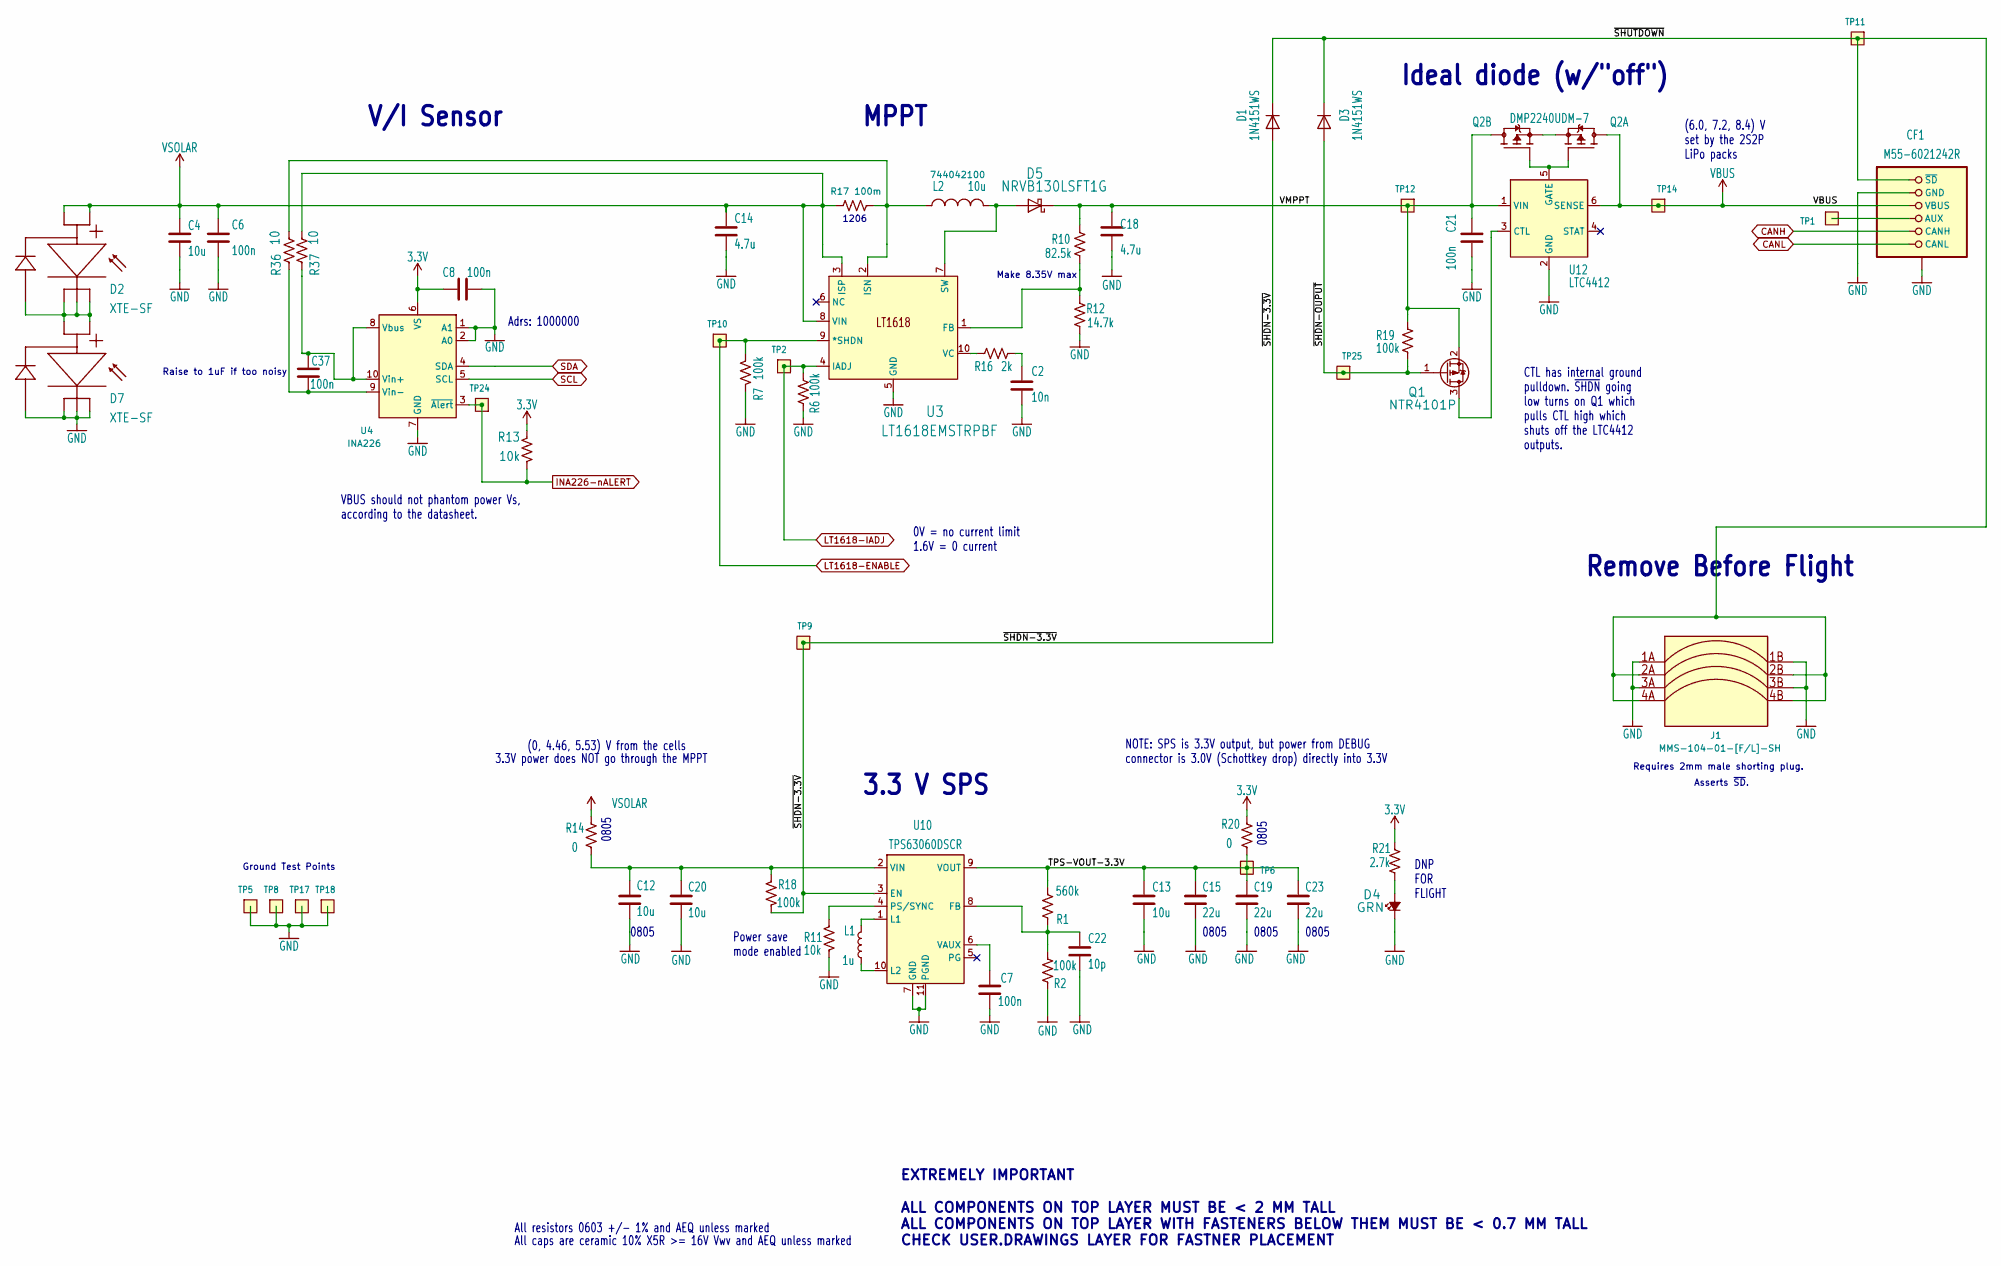
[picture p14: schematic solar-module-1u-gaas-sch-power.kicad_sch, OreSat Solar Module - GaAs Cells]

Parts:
C2: 10n; 0603-C-NOSILK; MPN C0603C103J3GECAUTO
C4, C13, C20: 10u; 0603-C-NOSILK; MPN GRT188R61C106KE13D
C6, C7, C8, C21, C37: 100n; 0603-C-NOSILK; MPN TMK107BJ104KAHT
C12: 10u; 0805-C-NOSILK; MPN GRT21BC71E106KE13L
C14, C18: 4.7u; 0603-C-NOSILK; MPN CL10A475KO8NNNC
C15, C19, C23: 22u; 0805-C-NOSILK; MPN 490-12389-2-ND
C22: 10p; 0603-C-NOSILK; MPN C0603C100J5GACAUTO
CF1: M55-6021242R; J-Harwin-M55-60X1242R; MPN M55-6021242R
D1, D3: 1N4151WS; D-SOD323-R; MPN 1N4151WS-E3-08
D2, D7: XTE-SF; SPECTROLAB-XTE-SF
D4: GRN; LED_0603_1608Metric; MPN 150060GS75000
D5: NRVB130LSFT1G; D_SOD-123; MPN NRVB130LSFT1G
J1: MMS-104-01-[F/L]-SH; SAMTEC-MMS-104-02-X-SH; MPN MMS-104-02-L-SH
L1: 1u; IND_1226AS-H-1R0N=P2; MPN 1227AS-H-1R0N=P2
L2: 10u; 744042100; MPN 744042100
Q1: NTR4101P; SOT-23; MPN NTR4101PT1G
Q2: DMP2240UDM-7; SOT-23-6; MPN DMP2240UDM-7
R1: 560k; 0603-C-NOSILK; MPN RMCF0603FT560K
R2, R6, R7, R18, R19: 100k; 0603-C-NOSILK; MPN RMCF0603FT100K
R10: 82.5k; 0603-C-NOSILK; MPN RMCF0603FT82K5
R11, R13: 10k; 0603-C-NOSILK; MPN RMCF0603FT10K0
R12: 14.7k; 0603-C-NOSILK; MPN RMCF0603FT14K7
R14, R20: 0; 0805-C-NOSILK; MPN ERJ-6GEY0R00V
R16: 2k; 0603-C-NOSILK; MPN RMCF0603FT2K00
R17: 100m; 1206-C; MPN CSR1206FTR100
R21: 2.7k; 0603-C-NOSILK; MPN RMCF0603FT2K70
R36, R37: 10; 0603-C-NOSILK; MPN RMCF0603FT10R0
TP1, TP2, TP5, TP6, TP8, TP9, TP10, TP11, TP12, TP14, TP17, TP18, TP24, TP25: TEST-POINT-LARGE-SQUARE; TestPoint-0.75mm-th
U3: LT1618EMSTRPBF; MSOP-10_MS; MPN IC REG BOOST ADJ 1.5A 10MSOP
U4: INA226; VSSOP-10_3x3mm_P0.5mm; MPN INA226AIDGST
U10: TPS63060DSCR; Texas_S-PWSON-N10; MPN IC REG BUCK BOOST ADJ 2A 10WSON
U12: LTC4412; TSOT-23-6; MPN LTC4412ES6#TRPBF

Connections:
3.3V: C8.1, R13.2, R20.1, R21.1, U4.6 (VS); also elsewhere on the board
/MPPT and Power/TPS-VOUT-3.3V: C13.1, C15.1, C19.1, C23.1, R1.2, R20.2, TP6.1, U10.9 (VOUT)
/MPPT and Power/VMPPT: C18.1, C21.1, D5.1 (K), Q1.2 (S), Q2.4 (D), R10.2, R19.2, TP12.1, U12.1 (VIN)
/MPPT and Power/~SHDN-3.3V: D1.2 (A), R18.1, TP9.1, U10.3 (EN)
/MPPT and Power/~SHDN-OUPUT: D3.2 (A), Q1.1 (G), R19.1, TP25.1
/MPPT and Power/~SHUTDOWN: CF1.1 (~SD), CF1.2 (~SD), D1.1 (K), D3.1 (K), J1.2A, J1.2B, J1.4A, J1.4B, TP11.1
CANH: CF1.9 (CANH), CF1.10 (CANH); also elsewhere on the board
CANL: CF1.11 (CANL), CF1.12 (CANL); also elsewhere on the board
GND: C2.2, C4.2, C6.2, C7.2, C8.2, C12.2, C13.2, C14.2, C15.2, C18.2, C19.2, C20.2, C21.2, C22.2, C23.2, CF1.3 (GND), CF1.4 (GND), CF1.P$1 (SHIELD), CF1.P$2 (SHIELD), CF1.P$3 (SHIELD), CF1.P$4 (SHIELD), D4.1 (K), D7.NEG1 (C1), D7.NEG2 (C2), D7.NEG3 (C3), D7.NEG4 (C4), J1.1A, J1.1B, J1.3A, J1.3B, R2.1, R6.2, R7.2, R11.1, R12.1, TP5.1, TP8.1, TP17.1, TP18.1, U3.5 (GND), U4.1 (A1), U4.2 (A0), U4.7 (GND), U10.7 (GND), U10.11 (PGND), U12.2 (GND); also elsewhere on the board
INA226-nALERT: R13.1, TP24.1, U4.3 (~Alert); also elsewhere on the board
LT1618-ENABLE: R7.1, TP10.1, U3.9 (*SHDN); also elsewhere on the board
LT1618-IADJ: R6.1, TP2.1, U3.4 (IADJ); also elsewhere on the board
unnamed: C2.1, R16.1
unnamed: CF1.7 (AUX), CF1.8 (AUX), TP1.1
unnamed: D2.NEG1 (C1), D2.NEG2 (C2), D2.NEG3 (C3), D2.NEG4 (C4), D7.POS1 (A1), D7.POS2 (A2)
unnamed: D4.2 (A), R21.2
unnamed: D5.2 (A), L2.2, U3.7 (SW)
unnamed: Q1.3 (D), U12.3 (CTL)
unnamed: Q2.1 (G), Q2.3 (G), U12.5 (GATE)
unnamed: Q2.2 (S), Q2.5 (S)
unnamed: R10.1, R12.2, U3.1 (FB)
unnamed: L2.1, R17.2, R36.1, U3.2 (ISN)
unnamed: R16.2, U3.10 (VC)
unnamed: C37.1, R37.1, U4.8 (Vbus), U4.10 (Vin+)
unnamed: C37.2, R36.2, U4.9 (Vin-)
unnamed: C22.1, R1.1, R2.2, U10.8 (FB)
unnamed: L1.2, U10.1 (L1)
unnamed: L1.1, U10.10 (L2)
unnamed: R11.2, U10.4 (PS/SYNC)
unnamed: C7.1, U10.6 (VAUX)
unnamed: C12.1, C20.1, R14.1, R18.2, U10.2 (VIN)
SCL: U4.5 (SCL); also elsewhere on the board
SDA: U4.4 (SDA); also elsewhere on the board
VBUS: CF1.5 (VBUS), CF1.6 (VBUS), Q2.6 (D), TP14.1, U12.6 (SENSE)
VSOLAR: C4.1, C6.1, C14.1, D2.POS1 (A1), D2.POS2 (A2), R14.2, R17.1, R37.2, U3.3 (ISP), U3.8 (VIN)

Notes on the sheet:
DNP FOR FLIGHT
0805
CTL has internal ground pulldown. ~{SHDN} going low turns on Q1 which pulls CTL high which shuts off the LTC4412 outputs.
(0, 4.46, 5.53) V from the cells
Ground Test Points
Make 8.35V max
Asserts ~{SD}.
Raise to 1uF if too noisy
All resistors 0603 +/- 1% and AEQ unless marked
NOTE: SPS is 3.3V output, but power from DEBUG connector is 3.0V (Schottkey drop) directly into 3.3V
Power save mode enabled
3.3 V SPS
EXTREMELY IMPORTANT ALL COMPONENTS ON TOP LAYER MUST BE < 2 MM TALL ALL COMPONENTS ON TOP LAYER WITH FASTENERS BELOW THEM MUST BE < 0.7 MM TALL CHECK USER.DRAWINGS LAYER FOR FASTNER PLACEMENT
MPPT
All caps are ceramic 10% X5R >= 16V Vwv and AEQ unless marked
Ideal diode (w/"off")
VBUS should not phantom power Vs, according to the datasheet.
3.3V power does NOT go through the MPPT
Remove Before Flight
V/I Sensor
0V = no current limit 1.6V = 0 current
1206
Adrs: 1000000
(6.0, 7.2, 8.4) V set by the 2S2P LiPo packs
Requires 2mm male shorting plug.

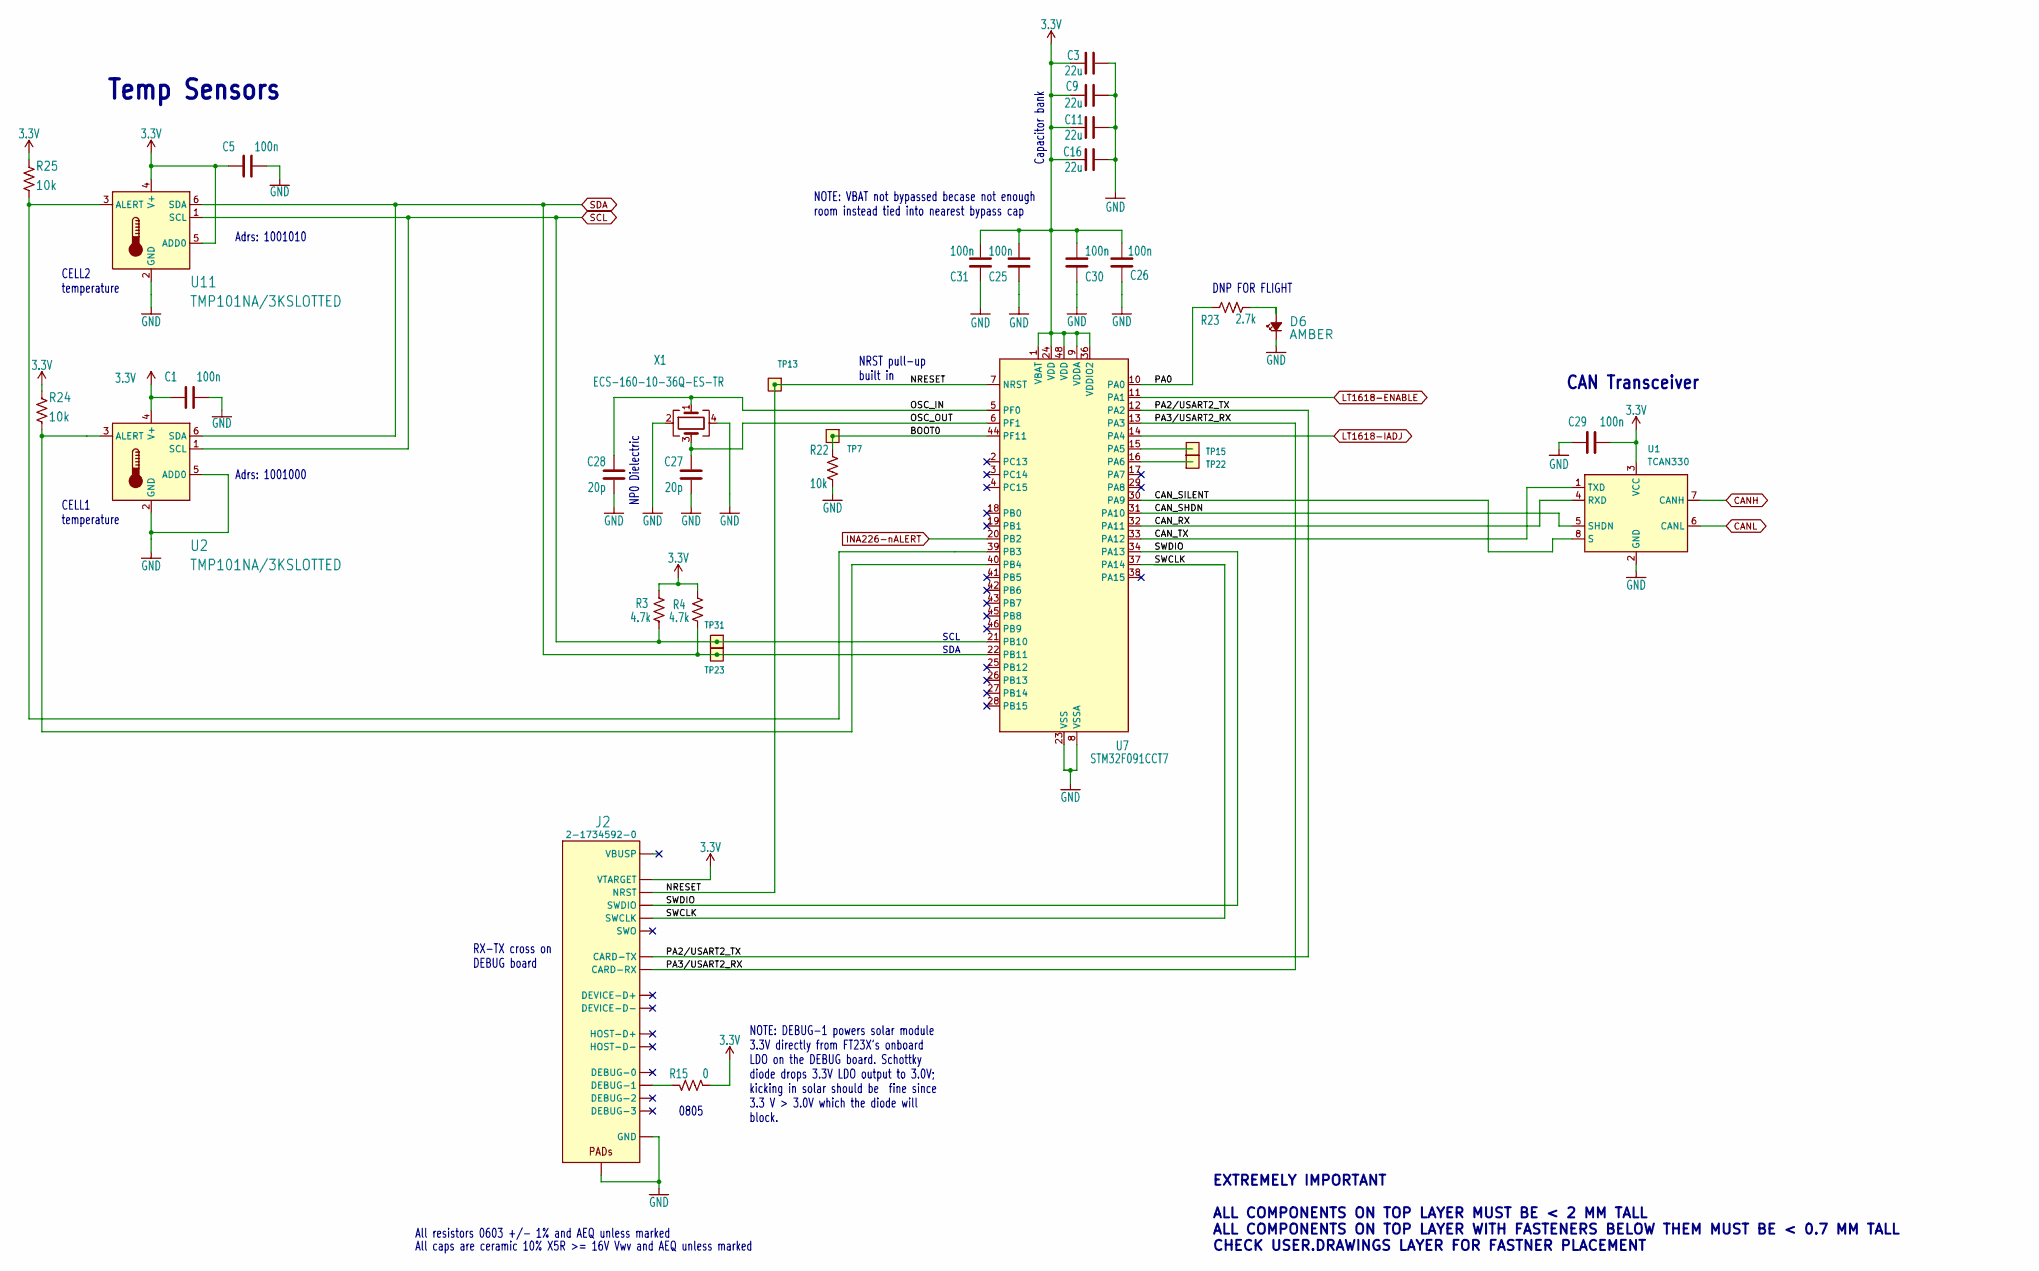
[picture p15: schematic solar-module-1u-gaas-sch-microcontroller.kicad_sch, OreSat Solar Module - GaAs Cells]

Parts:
C1, C5, C25, C26, C29, C30, C31: 100n; 0603-C-NOSILK; MPN TMK107BJ104KAHT
C3, C9, C11, C16: 22u; 0805-C-NOSILK; MPN 490-12389-2-ND
C27, C28: 20p; 0603-C-NOSILK; MPN C0603C200J5GACAUTO
D6: AMBER; LED_0603_1608Metric; MPN 150060AS75000
J2: 2-1734592-0; J-TE-2-1734592-0; MPN 2-1734592-0
R3, R4: 4.7k; 0603-C-NOSILK; MPN RMCF0603FT4K70
R15: 0; 0805-C-NOSILK; MPN ERJ-6GEY0R00V
R22, R24, R25: 10k; 0603-C-NOSILK; MPN RMCF0603FT10K0
R23: 2.7k; 0603-C-NOSILK; MPN RMCF0603FT2K70
TP7, TP13, TP15, TP22, TP23, TP31: TEST-POINT-LARGE-SQUARE; TestPoint-0.75mm-th
U1: TCAN330; SOT-23-8; MPN TCAN330GDCNT
U2, U11: TMP101NA/3KSLOTTED; DBV6-SLOT; MPN TMP101NA/3K
U7: STM32F091CCT7; LQFP-48_7x7mm_P0.5mm; MPN STM32F091CCT7TR
X1: ECS-160-10-36Q-ES-TR; MPN ECS-160-10-36Q-ES-TR

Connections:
3.3V: C1.1, C3.1, C5.1, C9.1, C11.1, C16.1, C25.2, C26.2, C29.2, C30.2, C31.2, J2.11 (VTARGET), R3.2, R4.2, R15.2, R24.2, R25.2, U1.3 (VCC), U2.4 (V+), U7.1 (VBAT), U7.9 (VDDA), U7.24 (VDD), U7.36 (VDDIO2), U7.48 (VDD), U11.4 (V+), U11.5 (ADD0); also elsewhere on the board
/Microcontroller/BOOT0: R22.1, TP7.1, U7.44 (PF11)
/Microcontroller/CAN_RX: U1.4 (RXD), U7.32 (PA11)
/Microcontroller/CAN_SHDN: U1.5 (SHDN), U7.31 (PA10)
/Microcontroller/CAN_SILENT: U1.8 (S), U7.30 (PA9)
/Microcontroller/CAN_TX: U1.1 (TXD), U7.33 (PA12)
/Microcontroller/NRESET: J2.10 (NRST), TP13.1, U7.7 (NRST)
/Microcontroller/OSC_IN: C28.1, U7.5 (PF0), X1.1
/Microcontroller/OSC_OUT: C27.1, U7.6 (PF1), X1.3
/Microcontroller/PA0: R23.2, U7.10 (PA0)
/Microcontroller/PA2/USART2_TX: J2.13 (CARD-TX), U7.12 (PA2)
/Microcontroller/PA3/USART2_RX: J2.12 (CARD-RX), U7.13 (PA3)
/Microcontroller/SWCLK: J2.15 (SWCLK), U7.37 (PA14)
/Microcontroller/SWDIO: J2.14 (SWDIO), U7.34 (PA13)
CANH: U1.7 (CANH); also elsewhere on the board
CANL: U1.6 (CANL); also elsewhere on the board
GND: C1.2, C3.2, C5.2, C9.2, C11.2, C16.2, C25.1, C26.1, C27.2, C28.2, C29.1, C30.1, C31.1, D6.1 (K), J2.3 (GND), J2.6 (GND), J2.9 (GND), J2.PAD1 (PAD), J2.PAD2 (PAD), R22.2, U1.2 (GND), U2.2 (GND), U2.5 (ADD0), U7.8 (VSSA), U7.23 (VSS), U7.35 (VSS), U7.47 (VSS), U11.2 (GND), X1.2, X1.4; also elsewhere on the board
INA226-nALERT: U7.20 (PB2); also elsewhere on the board
LT1618-ENABLE: U7.11 (PA1); also elsewhere on the board
LT1618-IADJ: U7.14 (PA4); also elsewhere on the board
unnamed: D6.2 (A), R23.1
unnamed: J2.18 (DEBUG-1), R15.1
unnamed: R24.1, U2.3 (ALERT), U7.40 (PB4)
unnamed: TP15.1, U7.15 (PA5)
unnamed: TP22.1, U7.16 (PA6)
unnamed: R25.1, U7.39 (PB3), U11.3 (ALERT)
SCL: R3.1, TP31.1, U2.1 (SCL), U7.21 (PB10), U11.1 (SCL); also elsewhere on the board
SDA: R4.1, TP23.1, U2.6 (SDA), U7.22 (PB11), U11.6 (SDA); also elsewhere on the board

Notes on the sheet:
Capacitor bank
SDA
Temp Sensors
NOTE: VBAT not bypassed becase not enough room instead tied into nearest bypass cap
DNP FOR FLIGHT
NRST pull-up built in
CAN Transceiver
NP0 Dielectric
NOTE: DEBUG-1 powers solar module 3.3V directly from FT23X's onboard LDO on the DEBUG board. Schottky diode drops 3.3V LDO output to 3.0V; kicking in solar should be fine since 3.3 V > 3.0V which the diode will block.
Adrs: 1001010
Adrs: 1001000
CELL2 temperature
RX-TX cross on DEBUG board
EXTREMELY IMPORTANT ALL COMPONENTS ON TOP LAYER MUST BE < 2 MM TALL ALL COMPONENTS ON TOP LAYER WITH FASTENERS BELOW THEM MUST BE < 0.7 MM TALL CHECK USER.DRAWINGS LAYER FOR FASTNER PLACEMENT
SCL
All resistors 0603 +/- 1% and AEQ unless marked
CELL1 temperature
0805
All caps are ceramic 10% X5R >= 16V Vwv and AEQ unless marked

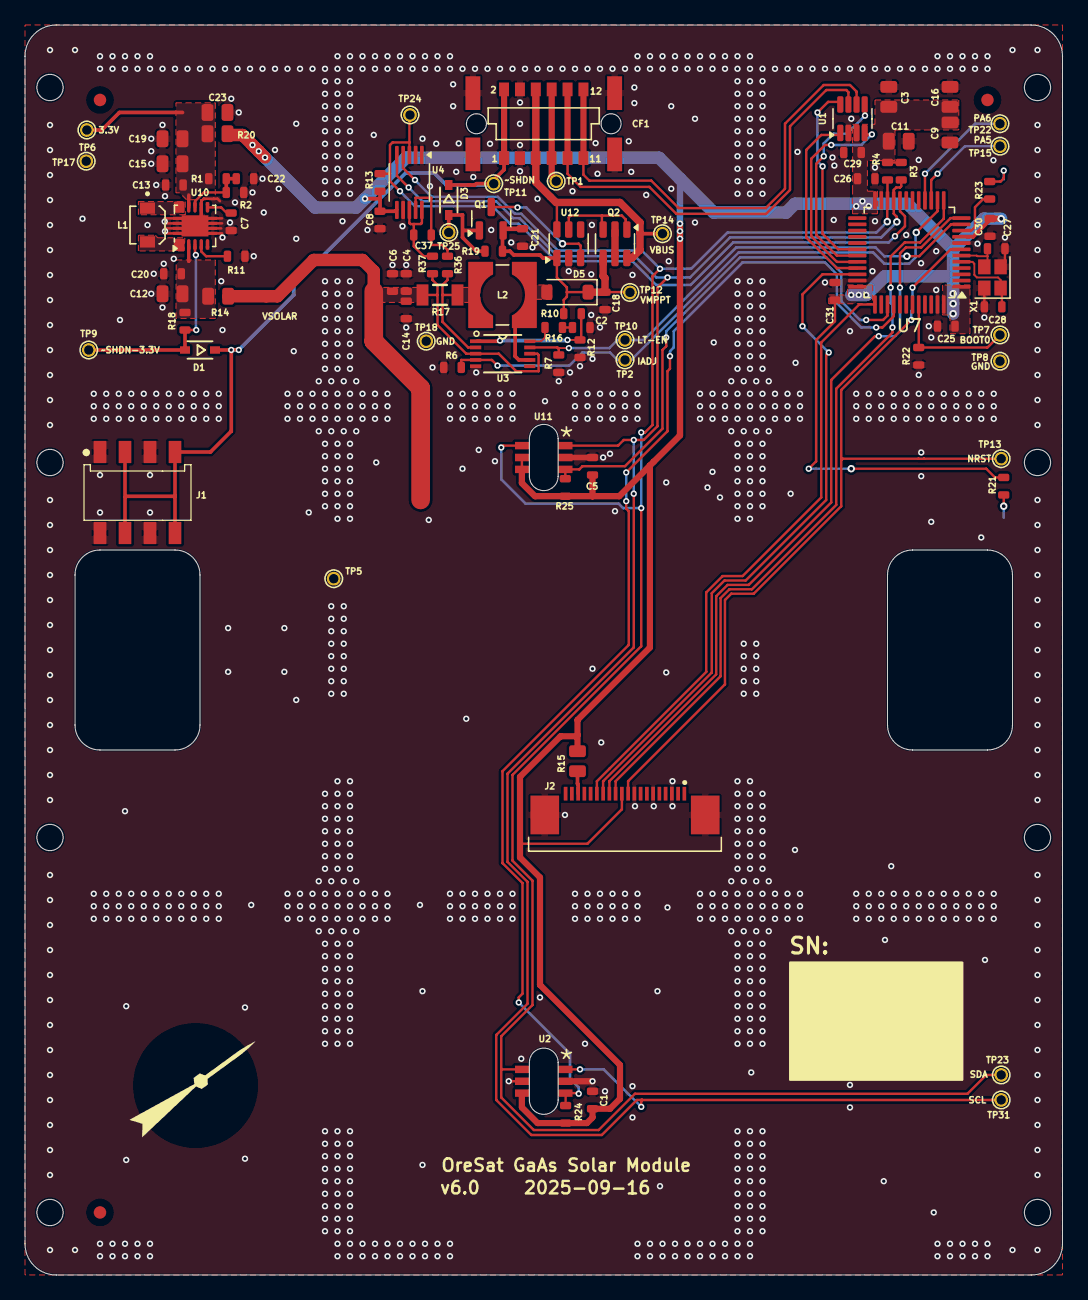
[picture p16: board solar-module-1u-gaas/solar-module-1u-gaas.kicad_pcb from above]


Board: 2 copper layers, 83.0 x 100.0 mm, 104 parts (7 on the bottom side), 54 nets.

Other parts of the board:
LOGO1: PSAS_LOGO_10X10
PCB1: ORESAT-SOLAR-BOARD-V1.0-SILICON-CELLS; ORESAT-SOLAR-BOARD-V4

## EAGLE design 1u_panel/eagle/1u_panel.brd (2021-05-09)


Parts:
C2: 10n; .0603-C-NOSILK; MPN UMK107B7103KAHT
C4, C13, C20: 10u; .0603-C-NOSILK; MPN GRT188R61C106KE13D
C6, C7, C8: 100n; .0603-C-NOSILK; MPN CL10B104KB85PND
C12: 10u; .0805-B-NOSILK; MPN GRT21BR61C106KE01L
C14, C18: 4.7u; .0603-C-NOSILK; MPN EMK107BBJ475KAHT
C15, C19, C23: 22u; .0805-B-NOSILK; MPN CL32B226KOJVPNE
C21: 100n; .0402-B-NOSILK; MPN CL10B104KB85PND
C22: 10p; .0603-C-NOSILK; MPN GRT188R61C106KE13D
CELL1, CELL2: XTE-SF 27.7cm2; SPECTROLAB-XTE-SF
CF1: HARWIN M55-6021242R; HARWIN-M55-60X1242R
D1, D3: 1N4151WS; SOD323-R
D4: GREEN; LED-0603; MPN IN-S63AT5A
D5: MBR0520L; SOD123; MPN NRVB130T3G
J1: SAMTEC-MMS-104-02-X-SHJ; SAMTEC-MMS-104-02-X-SH
L1: 1 uH; IND_1226AS-H-1R0N=P2; MPN VLS3010CX-1R5M-1
L2: 10u; NONSTANDARD; MPN 744042100
PCB1: ORESAT-SOLAR-BOARD-V4-SPECTROLABS; ORESAT-SOLAR-BOARD-V4
Q1: MOSFET-PCH-SOT23-6; SOT23-6; MPN DMP3050LVT-7
Q2: MOSFET-PCH-SOT23-6; SOT23-6; MPN DMP2240UDM-7
R1: 560k; .0603-C-NOSILK; MPN CRGCQ0603F470K
R2: 100k; .0603-C-NOSILK; MPN RR0816P-104-D
R6, R7, R18, R19: 100k; .0603-C-NOSILK; MPN RNCP0603FTD10K0
R9: 1M; .0603-C-NOSILK
R10: 82.5k; .0603-C-NOSILK; MPN ERA-3AEB8252V
R11: 10k; .0603-C-NOSILK
R12: 14.2k; .0603-C-NOSILK; MPN RN73R1JTTD1422D25
R13: NP; .0603-C-NOSILK; MPN RNCP0603FTD10K0
R14, R20: 0; .0805-C-NOSILK; MPN RMCF0805ZT0R00
R16: 2k; .0603-C-NOSILK; MPN RK73H1JTTD2001F
R17: 0.1 0805; .0805-C-NOSILK; MPN RMCF0805ZT0R00
R21: 2.7k; .0603-C-NOSILK; MPN CRGCQ0603F2K7
TP1, TP2, TP3, TP5, TP6, TP9, TP10, TP11, TP12, TP14, TP16, TP24, TP25, TP26, TP27, TP28, TP29: TEST-POINT-LARGE-SQUARE; 1X01
U3: LT1618EMSTRPBF; MSOP-10_MS; MPN LT1618EMS#TRPBF
U4: INA226AIDGSR; DGS10; MPN INA226AIDGSR
U10: TPS63060; CONV_TPS63060DSCT
U12: LTC4412; SOT23-6; MPN LTC4412ES6#TRPBF
U$1: FLIGHMARKERNEW; FLIGHTMARKER_NEW_BOARDS
U$2, U$3, U$4: FIDUCIAL; FIDUCIAL_1MM

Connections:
3.3V: C8.1, R20.1, R21.1, U4.6 (VS); also elsewhere on the board
4412-CTL: Q1.1 (D), Q1.2 (D), Q1.5 (D), Q1.6 (D), U12.3 (CTL)
4412-GATE: Q2.1 (G), Q2.3 (G), U12.5 (GATE)
!SHDN-3.3V: D1.A, R18.2, TP9.1, U10.3 (EN)
!SHDN-OUPUT: D3.A, Q1.3 (G), R19.1, TP25.1
!SHUTDOWN: CF1.1 (!SD), CF1.2 (!SD), D1.C, D3.C, J1.2A, J1.2B, J1.4A, J1.4B, TP11.1
AUX: CF1.7 (AUX), CF1.8 (AUX), TP1.1
CANH: CF1.9 (CANH), CF1.10 (CANH); also elsewhere on the board
CANL: CF1.11 (CANL), CF1.12 (CANL); also elsewhere on the board
GND: C2.2, C4.2, C6.2, C7.2, C8.2, C12.2, C13.2, C14.2, C15.2, C18.2, C19.2, C20.2, C21.2, C22.2, C23.2, CELL1.NEG1 (C1), CELL1.NEG2 (C2), CELL1.NEG3 (C3), CELL1.NEG4 (C4), CF1.3 (GND), CF1.4 (GND), CF1.P$1 (SHIELD), CF1.P$2 (SHIELD), CF1.P$3 (SHIELD), CF1.P$4 (SHIELD), D4.C, J1.1A, J1.1B, J1.3A, J1.3B, R2.1, R6.2, R7.1, R11.1, R12.1, U3.5 (GND), U4.1 (A1), U4.2 (A0), U4.7 (GND), U10.7 (GND), U10.11 (PGND), U10.12 (PGND), U10.13 (PGND), U10.14 (PGND), U10.15 (PGND), U10.16 (PGND), U10.17 (PGND), U10.18 (PGND), U10.19 (PGND), U12.2 (GND); also elsewhere on the board
INTERCELL: CELL1.POS1 (A1), CELL1.POS2 (A2), CELL2.NEG1 (C1), CELL2.NEG2 (C2), CELL2.NEG3 (C3), CELL2.NEG4 (C4)
LT1618-ENABLE: R7.2, TP10.1, U3.9 (*SHDN); also elsewhere on the board
LT1618-FB: R10.1, R12.2, U3.1 (FB)
LT1618-IADJ: R6.1, TP2.1, U3.4 (IADJ); also elsewhere on the board
LT1618-ISN: L2.P$1 (1), R17.2, TP5.1, U3.2 (ISN), U4.8 (VBUS), U4.9 (VIN-)
LT1618-SW: D5.A (ANODE), L2.P$2 (2), U3.7 (SW)
LT1618-VC: R16.2, U3.10 (VC)
unnamed: TP24.1, U4.3 (ALERT)
unnamed: C2.1, R16.1
unnamed: TP16.1, U12.4 (STAT)
unnamed: Q2.2 (S), Q2.5 (S)
unnamed: D4.A, R21.2
SCL: U4.5 (SCL); also elsewhere on the board
SDA: U4.4 (SDA); also elsewhere on the board
TPS-EN: R11.2, R13.1, TP29.1, U10.4 (PS/SYNC)
TPS-FB: C22.1, R1.1, R2.2, TP27.1, U10.8 (FB)
TPS-L1: L1.1, U10.1 (L1)
TPS-L2: L1.2, U10.10 (L2)
TPS-PG: R9.1, TP26.1, U10.5 (PG)
TPS-VAUX: C7.1, TP28.1, U10.6 (VAUX)
TPS-VIN: C12.1, C20.1, R13.2, R14.1, R18.1, U10.2 (VIN)
TPS-VOUT-3.3V: C13.1, C15.1, C19.1, C23.1, R1.2, R9.2, R20.2, TP6.1, U10.9 (VOUT)
VBUS: CF1.5 (VBUS), CF1.6 (VBUS), Q2.6 (D), TP14.1, U12.6 (SENSE)
VMPPT: C18.1, C21.1, D5.K (CATHODE), Q1.4 (S), Q2.4 (D), R10.2, R19.2, TP12.1, U12.1 (VIN)
VSOLAR: C4.1, C6.1, C14.1, CELL2.POS1 (A1), CELL2.POS2 (A2), R14.2, R17.1, TP3.1, U3.3 (ISP), U3.8 (VIN), U4.10 (VIN+)

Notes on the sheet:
2x Spectrolabs XTE-SF 27cm^2 CIC - Voc = 5.50 V - Vmp = 4.87 V - Isc = 502 mA - Imp = 480 mA
OreSat Solar Board: MPPT + PWR
5.1
V/I Sensor
MPPT
All resistors 0603 +/- 1% unless marked
All caps are ceramic 10% X5R >= 16V Vwv unless marked
0805
(0, 4.87, 5.50) V from the 2 cells
(6.0, 7.2, 8.4) V set by the 2S2P LiPo packs
3.3 V SPS
VBUS should not phantom power Vs, according to the datasheet.
Adrs: 1000000
CTL has internal ground pulldown. !SHDN going low turns on Q1 which pulls CTL high which shuts off the LTC4412 outputs.
ALL COMPONENTS MUST BE < 2.0 MM TALL
ALL COMPONENTS ABOVE FASTENERS MUST BE < 0.7 MM TALL
3.3V power does NOT go through the MPPT
Must be < 0.7 mm tall due to fasteners
0V = no current limit 1.6V = 0 current
NOTE: SPS is 3.3V output, but power from DEBUG connector is 3.0V (Schottkey drop) directly into 3.3V
Solar Cells
Ideal diode (w/"off")
Remove Before Flight
ONLY POPULATED IN +Z+X SOLAR BOARD. DNP ALL OTHER BOARDS. Requires 2mm male shorting plug.
DNP FOR FLIGHT
Power save mode enabled


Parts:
C1, C5, C25, C26, C29, C30, C31: 100n; .0603-C-NOSILK; MPN CL10B104KB85PND
C3, C9, C11, C16: 22u; .0805-B-NOSILK; MPN CL32B226KOJVPNE
C27, C28: 20p; .0603-C-NOSILK; MPN GCM1885C2A200JA16D
D6: AMBER; LED-0603; MPN IN-S63AT5A
J2: ORESAT-DEBUG-CONNECTOR-ALL; TE_2-1734592-0; MPN 687120183622
R3, R4: 4.7k; .0603-C-NOSILK; MPN RE0603FRE074K7L
R15: 0; .0805-C-NOSILK; MPN RMCF0805ZT0R00
R22: 10k; .0603-C-NOSILK; MPN CRGCQ0603F2K7
R23: 2.7k; .0603-C-NOSILK; MPN CRGCQ0603F2K7
R24, R25, R26, R27: 1k/NP; .0603-C-NOSILK; MPN CR0603AFX-1001ELF
TP4, TP7, TP8, TP13, TP15, TP17, TP18, TP19, TP20, TP21, TP22, TP23, TP30, TP31: TEST-POINT-LARGE-SQUARE; 1X01
U1: TCAN330; SOT23-8_TI-DCN; MPN TCAN330GDCNT
U2, U11: TMP101NA/3KSLOTTED; DBV6-SLOT; MPN TMP101NA/3K
U7: STM32F091C; MPN STM32F091CCT6TR
X1: 16MHZ-2.5x2mm; CRYSTAL_2.5X2; MPN ECS-160-10-36Q-ES-TR

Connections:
3.3V: C1.1, C3.1, C5.1, C9.1, C11.1, C16.1, C25.2, C26.2, C29.2, C30.2, C31.2, J2.11 (VTARGET), R3.2, R4.2, R15.1, U1.3 (VCC), U2.1 (V+), U7.1 (VBAT), U7.9 (VDDA), U7.24 (VDD), U7.36 (VDDIO2), U7.48 (VDD), U11.1 (V+), U11.2 (ADD0); also elsewhere on the board
BOOT0: R22.1, TP7.1, U7.44 (PF11-BOOT0)
CANH: U1.7 (CANH); also elsewhere on the board
CANL: U1.6 (CANL); also elsewhere on the board
CAN_RX: U1.4 (RXD), U7.32 (PA11)
CAN_SHDN: U1.5 (SHDN), U7.31 (PA10)
CAN_SILENT: U1.8 (S), U7.30 (PA9)
CAN_TX: U1.1 (TXD), U7.33 (PA12)
DEBU-1/SOLAR3V: J2.18 (DEBUG-1), R15.2, TP18.1
DEBUG-0: J2.17 (DEBUG-0), TP17.1
DEBUG-2: J2.19 (DEBUG-2), TP19.1
DEBUG-3: J2.20 (DEBUG-3), TP20.1
GND: C1.2, C3.2, C5.2, C9.2, C11.2, C16.2, C25.1, C26.1, C27.2, C28.2, C29.1, C30.1, C31.1, D6.C, J2.3 (GND), J2.6 (GND), J2.9 (GND), J2.PAD1 (PAD), J2.PAD2 (PAD), R22.2, R24.2, R25.2, R26.2, R27.2, U1.2 (GND), U2.2 (ADD0), U2.5 (GND), U7.8 (VSSA), U7.23 (VSS), U7.35 (VSS), U7.47 (VSS), U11.5 (GND), X1.2 (SHIELD), X1.4 (SHIELD); also elsewhere on the board
LT1618-ENABLE: U7.11 (PA1); also elsewhere on the board
LT1618-IADJ: U7.14 (PA4); also elsewhere on the board
unnamed: J2.1 (VBUSP), J2.2 (VBUSP), TP8.1
unnamed: TP4.1, U2.6 (ALERT)
unnamed: TP30.1, U11.6 (ALERT)
unnamed: D6.A, R23.1
NRESET: J2.10 (NRST), TP13.1, U7.7 (NRST)
PA0: R23.2, U7.10 (PA0)
PA2/USART2_TX: J2.13 (CARD-TX), U7.12 (PA2)
PA3/USART2_RX: J2.12 (CARD-RX), U7.13 (PA3)
PA5: TP15.1, U7.15 (PA5)
PA6: TP22.1, U7.16 (PA6)
SCL: R3.1, TP31.1, U2.4 (SCL), U7.21 (PB10), U11.4 (SCL); also elsewhere on the board
SDA: R4.1, TP23.1, U2.3 (SDA), U7.22 (PB11), U11.3 (SDA); also elsewhere on the board
SMSN0: R24.1, U7.25 (PB12)
SMSN1: R25.1, U7.26 (PB13)
SMSN2: R26.1, U7.27 (PB14)
SMSN3: R27.1, U7.28 (PB15)
SWCLK: J2.15 (SWCLK), U7.37 (PA14-SWCLK)
SWDIO: J2.14 (SWDIO), U7.34 (PA13-SWDIO)
SWO: J2.16 (SWO), TP21.1
XTAL1-IN: C28.1, U7.5 (PF0-OSC_IN), X1.1
XTAL1-OUT: C27.1, U7.6 (PF1-OSC_OUT), X1.3 (2)

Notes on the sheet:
Temp Sensors
Adrs: 1001010
NRST pull-up built in
CAN Transceiver
NOTE: VBAT not bypassed becase not enough room instead tied into nearest bypass cap
RX-TX cross on DEBUG board
NOTE: Does not have access to I2C emergency bootstrapping
Adrs: 1001000
NP0 Dielectric
0805
NOTE: DEBUG-1 powers solar module 3.3V directly from FT23X's onboard LDO on the DEBUG board. Schottky diode drops 3.3V LDO output to 3.0V; kicking in solar should be fine since 3.3 V > 3.0V which the diode will block.
CELL1 temperature
CELL2 temperature
DNP FOR FLIGHT
OreSat Solar Board: Microcontroller
Capacitor bank
Solar module Serial Number Required by CAN messages. 0: +X+Z 1: -Y+Z 2: -X+Z 3: -Y+Z 4: +X-Z .. and so on.



Board: 2 copper layers, 83.0 x 100.0 mm, 112 parts (4 on the bottom side), 63 nets.

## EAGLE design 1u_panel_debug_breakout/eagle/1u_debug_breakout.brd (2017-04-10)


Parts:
J1: 1.27MM-SWD-CONNECTOR; 1.27MM_2X5
JP2: PINHD-1X8; 1X08
JP3: PINHD-1X6; 1X06
LED1: LEDCHIPLED_0603; CHIPLED_0603
R1: R-US_R0603; R0603
S1: TL3302BF180QG/TR; TL3302_GULL_WING
U$1: 2MM-1X8-M; CF-2MM-1X8-PRECIDIP-880

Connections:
3V3: J1.VTREF, JP2.2, U$1.2
DEBUG: JP2.8, R1.2, U$1.8
GND: J1.GND, J1.GND@2 (GND), JP2.1, JP3.1, LED1.C, S1.2, U$1.1
unnamed: LED1.A, R1.1
RESET: J1.!RESET, JP2.3, S1.1, U$1.3
SWCLK: J1.SWDCLK (SWDCLK/TCK), JP2.4, U$1.4
SWDIO: J1.SWDIO (SWDIO/TMS), JP2.5, U$1.5
USART2_RX: JP2.7, JP3.5, U$1.7
USART2_TX: JP2.6, JP3.4, U$1.6

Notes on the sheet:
OreSat 1U Solar Panel Debug Breakout


Board: 2 copper layers, 36.0 x 24.0 mm, 7 parts (0 on the bottom side), 9 nets.

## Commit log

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2016-01-27 Deleted extraneous files, updated schema symbol for SPV1040 because pretty. Removed other addressed modules. Added button for xshut for testing.
    [Solar_Array.sch]
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2016-01-28 Removed extraneous circuitry, added more component values, swapped 1x2 conn with 1x3 conn.
    [Solar_Array.sch]
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2016-02-10 Fixed voltage divider from SPV1040, Added Vctrl Divider component values, added Shunt to Vout of 1040, added TVS to PV in and to output bus.
    [Solar_Array.sch]
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2016-02-13 Finished footprints for SPV1040, LTC2990, TVS Diodes, generated netlist. Initial PCB config finished.
    [Solar_Array.kicad_pcb, Solar_Array.sch, _saved_Solar_Array.sch]
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2016-02-19 Fixed missing/broken ground.
    [Solar_Array.kicad_pcb]
2016-02-24 Reduced size of PCB layout to 3 cm
    -Moved components
    -Generated updated drill files
    -Generated Gerb files
    -Updated Notes on Cell power on schematic sheet.
    [Solar_Array.kicad_pcb, Solar_Array.sch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]
2016-03-03 Changed Design Rules, created BOM
    *Changed global trace width allowances to .1 mm
    *Adjusted settings on pad width/length of ltc2990 footprint.
    [BOM.ods, Solar_Array.kicad_pcb]
2016-03-03 Rebuilt LTC2990 footprint. Regenerated Gerb Files -Changed LTC2990 pad width from .334 to .305 -Replaced old footprint and generated gerb files note that design check passed without warnings.
    [Solar_Array.kicad_pcb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]
2016-03-04 Updated Design Rules, generated new gerb files. -Fixed issues with soldermask relief. -Fixed issues with pad relief. -Regenerated f.paste, b.paste, f.mask, b.mask gerber files -
    [Solar_Array.kicad_pcb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]
2016-03-09 Fixed glaring errors in layout. Changed footprints.
    -Fixed LTC2990 and SPV1040 footprints to reflect phsical layout
    -Fixed board layout to accomodate actual design.
    [Solar_Array.kicad_pcb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]
2016-03-09 Added test points. Removed Shotkey.
    -Added test points to PVin, VCC and Vout.
    -Removed potentially uneccesary shotkey diodes.
    -Increased width of SPV1040 pads.
    -Generally cleaned up traces on board.
    -Updated 3d Model of various footprints in Solar Libs.
    [Solar_Array.kicad_pcb, Solar_Array.sch]
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2016-03-30 Created Rev 1 -Added several new filter caps. -Added more accurate inductor values. -Added Current limiting resistor. -Updated all component values to reflect functioning values.
    [Solar_Array_Rev1.sch]
2016-03-31 Created Libs, Finished PCB Layout. -Created Solar_Array lib. -Finished layout for rev 1.0
    [Solar_Array_Rev1-B.Cu.gbr, Solar_Array_Rev1-B.Paste.gbr, Solar_Array_Rev1-B.SilkS.gbr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]
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2016-04-09 Added PDF's and generated SVG's. Updated Component values.
    -Fixed mixing capacitor values on board layout.
    -Added 'PDF' folder to docs
    -Generated svg and pdf's of project
    [Solar_Array_Rev1.kicad_pcb]
2016-04-11 Updated component vals. Added filter Caps, TVS array
    -Updated and used //47uF for in/out filters.
    -Added more robust shutdown. XShut tied to input.
    -Introduced TVS array on schematics.
    [Solar_Array_Rev1.sch]
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2016-04-12 Added components, updated BOM -Added parallel filter cap input. -Updated BOM to reflect new parts.
    [Rev1_BOM.ods, Solar_Array_Rev1.sch]
2016-04-13 Removed old files, repaired broken schema, finished layout.
    -Removed old SVG DRL and GBR files
    -Removed old PDF files
    -Fixed broken TVS_4x4 Schematic and updated footprint
    -PCB file created
    -Board layout finished
    [Rev1_BOM.ods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]
2016-04-16 Removed D2. Set R9 as NP resistor and tied sensor to R5.
    [Solar_Array_Rev1.kicad_pcb, Solar_Array_Rev1.sch]
2016-04-23 Optimized for power. -Changed Vctrl divider on SPV1040 to limit power dissipation and current. -Removed needlessly large input capacitor. -Lowered cap value to recommended values near temp sensing tr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
    [Solar_Array_Rev1.kicad_pcb, Solar_Array_Rev1.sch]
2016-04-24 Finished Layout, updated notes, regenerated PDF's - Finished the board layout with obnoxious stitching. - Updated component notes for IC's - Regenerated F/B copper PDF's and schema PDF's
    [Solar_Array_Rev1.sch]
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2016-05-28 Created Schematics, Added Current Sense Circuitry -Created microcontroller schematic symbol -Created sense comparator schematic -Updated design with correct symbols -Added PV in/out -Calculated and s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
    [Solar_Array_Rev4.sch]
2016-06-01 Assigned Pin functions to ST microcontroller. -Found CAN TX/RX and assigned. -Found ADC in's for voltage/current sense. -Found TIM1 chn 1/3 for PWM control
    [Solar_Array_Rev4.sch]
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2016-06-11 Rev1 GERBS. Rev 4 Schematic editing/placement. -Regenerated rev1 gerbs -Added/updated schematic symbols for LDO, Crystal, CAN, uC -Added decoupling caps to various inputs -Reworked schematics because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
    [Solar_Array_Rev1.kicad_pcb, Solar_Array_Rev4.sch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]
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2016-06-18 Updated schematic values, regenerated netlist, reassigned footprints, added components.
    -Added 5th cap to input/output cap array.
    -Added schematic drawing of solar cells.
    -Added Schematic drawing of 40pin header.
    -Updated component footprint assignments for caps.
    -Reorganized drawing to accomodate larger size.
    [Solar_Array_Rev1.kicad_pcb, Solar_Array_Rev1.sch]
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2016-06-24 Added Mechanical drawings/folder. Finished layout. -Added /mechanical to /solar -Added solar stl -Finished layout
    [Solar_Array_Rev1.kicad_pcb, Solar_Panel_1U.stl]
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2016-06-27 Started transcription from kicad to Eagle -Added RCL to board -Added stand-in parts for p/n fets -Started nets.
    [1u_panel.brd, 1u_panel.sch, Solar_Array_Rev1.kicad_pcb]
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2016-07-27 Finished topological layout. Fixed polygons, replaced caps and other passives, replaced connector.
    [1u_panel.brd, 1u_panel.sch]
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2016-07-30 Added giant cutouts for umbilicals. Wow, sometimes using the same thing over and over sucks :)
    [1u_panel.brd]
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2016-09-28 Set STM32 Symbol on correct grid (2.54mm)
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2016-10-17 Pushing changes from Space Electronics workshop - no more TVS diodes, need onboard regulator, etc.
    [1u_panel.brd, 1u_panel.sch]
2016-10-19 Added LM3761, removed TPS arrays, adjusted schematic symbols to clean up drawings
    [1u_panel.brd, 1u_panel.sch]
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2016-10-28 Fixed forward/back annotation errors. Yay.
    [1u_panel.brd, 1u_panel.sch]
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2016-10-28 Fixed and adjusted various problem packages.
    [1u_panel_bkup.brd]
2016-11-02 Finished board layout, fixed upside-down NPN pinout.
    [1u_panel.brd, 1u_panel.sch]
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2016-11-06 Lots o' changes: Moved to the TCAN330 can controller. Looked for a new SPS chip, but Austin found a really good one, couldn't justify switching to a lower power one in a smaller package because 0.5 m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
    [1u_panel.brd, 1u_panel.sch, list-of-stm32f0-processors.xls]
2016-11-06 Added new OreSat connector. IMPORTANT: not in the right place yet, still waiting on Calvin for vertical height. Switched from QFN to LQFP just because we have the room. Did a bit of component placeme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
    [1u_panel.brd, 1u_panel.sch]
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2016-11-13 v1 solar array. Minor cleanup on the SPV inductor left, but not critical. Moved to two layers, cleaned up polygons, added stiching vias, tightened up, moved tnames around, and basic OCD cleanup.
    [1u_panel.brd, 1u_panel.sch]
2016-11-13 Wanted more ground, so reduced slots in solar array by 1 mm on the top and bottom.
    [1u_panel.brd]
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2016-11-26 Decided to double check the components calculates and inso fell into a deep rabbit hole. So, so many rabbits. See the google doc, which should become a markdown file soon, which shows the changes in 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
    [1u_panel.brd, 1u_panel.sch]
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2016-12-17 Moved alta solar module footprint into this repo. Updated with bent tabs. Modified PCB cutouts to give more room for module encapsulation. moved from standard ARM debug connector to RA 2mm female hea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
    [1u_panel.brd, 1u_panel.sch]
2016-12-17 Minor fix on board gnd polygon
    [1u_panel.brd]
2016-12-17 Mild cleanup: better stapling, moved positive PV rail above connector for better ground... aaaaand discovered that the connector is going to hit the aluminum frame. Whoops.
    [1u_panel.brd]
2016-12-18 Updated tkeepout and cutouts based on Calvin's feedback that it's actually 5.5mm, not 6mm, on the left and right edges.
    [1u_panel.brd]
2016-12-31 OK can this be the last mod before we send this off? Please? New tab configuration goes through board slots and then bends around, lots of wins hopefully for strain relief and better current paths. N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
    [1u_panel.brd, 1u_panel.sch]
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2017-01-23 Changed Alta Cell to be 90.5 mm long; the datasheet is ALWAYS right :)
    [1u_panel.brd, 1u_panel.sch]
2017-02-05 Created formal BOM. In the process, fixed attributes on all of the parts in the schematic. Cleared some uncleared DRCs on the board (how did that happen?). Otherwise, no changes to the board file. Fi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
    [1u_panel.brd, 1u_panel.sch, 1u_panel.xlsx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]
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2017-02-06 Fixing component errors; Q1 is an SOT-23 not an SC-70, some components were out of stock, had wrong attributes, etc. BOM is now mostly error free.
    [1u_panel.brd, 1u_panel.sch, 1u_panel.xlsx]
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2017-03-05 Whoops, wrong place for BOM, also updated NP to DNP.
    [1u_panel.xlsx, BOM.ods, Rev1_BOM.ods]
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2017-05-20 Changed sensor cap to correct value on schematic. Added missing 10k PB8-BOOT pin.
    [1u_panel.brd, 1u_panel.sch]
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2018-01-31 Begin v2 solar panel work. Move to the ZSPM4521 MPPT IC which we hope is on its way despite the EOL, move to the TPS63070x buck-boost converter so we can go from 2 to 12 V for the 3.3V supply, add LT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
    [1u_panel.brd, 1u_panel.sch]
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2018-02-19 v2 solar panels 95% done. No airwires, but TNAMES still needs cleanup, there needs more stapling, and the whole solder mask issue needs to be worked out. Yeesh, how we gonna do that?
    [1u_panel.brd, 1u_panel.sch]
2018-02-22 Fixed TSTOP on non-ground by making passageways for the signals. Fixed tnames.
    [1u_panel.brd, 1u_panel.sch]
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2018-02-22 More stapling, switched to 2 layer (doesn't need to be 4), aligned tnames, ready for fab.
    [1u_panel.brd]
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2018-02-25 Fixed some attributes on parts.
    [1u_panel.brd, 1u_panel.sch]
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2018-02-26 Fixed breakout connector to solar panel, added scope clips.
    [1u_debug_breakout.brd, 1u_debug_breakout.sch, 1u_panel_breakout.brd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]
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2018-10-07 Added latest DXF drawing to board. Added some radii, cleaned up board layers, still need to fix the main solar connector to the TH part.
    [1u_panel.brd, 1u_panel.sch]
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2019-07-21 fixed screw up on can layout
    [1u_panel.brd]
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2019-07-25 Fixed I2C lines from STM32, moved 3.3V system to work right off of the solar panel instead of after the MPPT, some routing clean up. Left to do: stitching, polish, and figure out about the damn debug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
    [1u_panel.brd, 1u_panel.sch]
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2019-07-29 Switched debug port to a FFC (yes we'll regret this but c'est la vie), fixed MAX pin, cleanup, stiching, last minute checks.
    [1u_panel.brd, 1u_panel.sch]
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2019-08-22 fixed the shdn line through the tstop
    [1u_panel.brd]
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2019-10-12 Added correct wavelength ratios into driver
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2020-01-24 fixed silkscreen bug
    [SolarSimulatorPanel.brd, SolarSimulatorPanel.sch]
2020-01-25 fixed solder mask so vias are tented on solar simulator
    [SolarSimulatorPanel.brd]
2020-01-27 Final cleanup! Moved things around for final cleanup, fixed BOM via oresat-rcl, etc.
    [SolarSimulatorPanel.brd, SolarSimulatorPanel.sch]
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2020-06-30 added 0 ohm jumpers to isolate certain blocks, moved debug to vout, grounded boot0, added note about screwhead avoidance, layout tweaks, added indicatr LED on 3.3V line
    [1u_panel.brd, 1u_panel.sch]
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2020-07-23 Updated to official solar board connector. Fixed frame versions and labels. No significant changes, still version 5.
    [1u_panel.brd, 1u_panel.sch]
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2020-07-23 Fixed bizarre inconsistancy error?
    [1u_panel.brd, 1u_panel.sch]
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2020-11-03 fixed tcream for debug and updated bom
    [1u_panel.brd, 1u_panel.sch, 1u_panel_BOM.xlsx]
2020-12-06 swapped 3.3V sps to the tps63060 because supply chains are hard
    [1u_panel.brd, 1u_panel.sch]
2020-12-06 fixed wonky ground on tps63060
    [1u_panel.brd, 1u_panel.sch]
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2020-12-21 Ugh, forgot to check in -- Fixed some random stubs, updated date, other polish?
    [1u_panel.brd, 1u_panel.sch]
2021-01-08 Q1 had the wrong part number! Fixed.
    [1u_panel.brd, 1u_panel.sch]
2021-01-12 Finally fixed the LTC4412 solder mask on Pin 2. Finally.
    [1u_panel.brd, 1u_panel.sch]
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2021-03-22 V5.2, fixed temp sensors AGAIN, and added fiducials
    [1u_panel.brd, 1u_panel.sch]
2021-03-26 ACTUALLY FIXED THE TEMP SENSORS I SWEAR
    [1u_panel.brd, 1u_panel.sch]
2021-04-18 v5.3 solar boards. Now with fiducials, a more direct cap bank, cleaned up 3.3V SPS area, and minor other little fixes.
    [1u_panel.brd, 1u_panel.sch, 1u_panel_BOM.xlsx]
2021-05-09 Fixed part number on 3.3V buck-boost - should have been the TPS63060.
    [1u_panel.brd, 1u_panel.sch]
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2023-05-02 Cleaned up schematic; added correct values and part numbers, added datasheet links to important components, imported sch to brd, LOTS of errors to clean up there but it's at synced now.
    [1u_panel.kicad_pcb, MPPT_%2f_PWR.kicad_sch, Microcontroller.kicad_sch]
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2023-05-28 Update test-plan.md
    Updated charging voltage to the correct value.
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2023-05-29 Update test-plan.md
    Updated solar module current draw error range based on data acquired from testing 9 modules.
2023-05-29 Fixed R12 value to make VOUT to 8.4V max. Was at 8.6V max. Also cleaned up some EAGLE import issues, mostly text size and labels.
    [1u_panel-microcontroller.kicad_sch, 1u_panel-power.kicad_sch, 1u_panel.kicad_sch]
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2024-08-19 fixed board outline, title blocks
    [1u_panel-cells.kicad_sch, 1u_panel-microcontroller.kicad_sch, 1u_panel-power.kicad_sch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]
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2024-09-30 Polish on Jack's final design. Swapped out rectangles for zones on multiple layers, cleaned up a lot of small layout bits, fixed some mechanical crashes with screw heads, fixed up the silk screen, an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
    [1u_panel-cells.kicad_sch, 1u_panel-microcontroller.kicad_sch, 1u_panel-power.kicad_sch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]
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2025-03-04 chages for https://github.com/oresat/oresat-solar-hardware/issues/53
    [1u_panel-cells.kicad_sch, 1u_panel-microcontroller.kicad_sch, 1u_panel-power.kicad_sch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]
2025-05-18 changes for bringup issues on Si Solar module
    [1u_panel-cells.kicad_sch, 1u_panel-microcontroller.kicad_sch, 1u_panel-power.kicad_sch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]
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2025-09-16 Adding v6.0 GaAs module based off of the v1.1 silicon module, which fixes so many issues it's not even worth upgrading the old v5.3 GaAs module. Still needs new mounting tape and cell backside contac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
    [solar-module-1u-gaas-sch-microcontroller.kicad_sch, solar-module-1u-gaas-sch-power.kicad_sch, solar-module-1u-gaas.kicad_pcb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]
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2025-09-18 Fixed ERC errors, including unused blocks and some power stuff.
    [solar-module-1u-si-sch-microcontroller.kicad_sch, solar-module-1u-si-sch-power.kicad_sch]
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2025-09-21 Finished routing, starting on fixing DRC
    [solar-module-1u-si-sch-microcontroller.kicad_sch, solar-module-1u-si.kicad_pcb]
2025-09-21 Fixed most DRC errors
    [solar-module-1u-si-sch-power.kicad_sch, solar-module-1u-si.kicad_pcb]
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2025-09-22 D1 and D3 footprints updated, moved debug connector, added additional power vias, moved temp sensors from screw holes, fixed silkscreen
    [solar-module-1u-si-sch-power.kicad_sch, solar-module-1u-si.kicad_pcb]
2025-09-24 Final polishing before fab. Fixed I2C pullups, removed some silly test points, lots of good zone planning on layer 3, cleaned up solar ideal diodes, moved LED to a blink light instead of power light.
    [solar-module-1u-si-sch-cells.kicad_sch, solar-module-1u-si-sch-microcontroller.kicad_sch, solar-module-1u-si-sch-power.kicad_sch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]
2025-09-24 Fix up BOM
    [solar-module-1u-si-sch-cells.kicad_sch, solar-module-1u-si-sch-microcontroller.kicad_sch, solar-module-1u-si-sch-power.kicad_sch]
2025-10-21 Fixed small issue in MCXN symbol
    [solar-module-1u-si-sch-microcontroller.kicad_sch]
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2026-02-23 Solar Module with GaAs Cells and MCXN processor v1.1
    Fixed BOM, fixed solar connector sync between brd/sch, routed UART lines to the connector, untented vias for venting. Sent to fab.
    [solar-module-1u-gaas-sch-cells.kicad_sch, solar-module-1u-gaas-sch-microcontroller.kicad_sch, solar-module-1u-gaas-sch-power.kicad_sch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]
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

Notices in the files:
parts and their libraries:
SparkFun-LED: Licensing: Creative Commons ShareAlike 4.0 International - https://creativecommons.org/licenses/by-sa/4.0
